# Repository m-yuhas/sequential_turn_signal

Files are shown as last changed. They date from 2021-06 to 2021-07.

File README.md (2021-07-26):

# Sequential Turn Signal
[中文指南](https://github.com/m-yuhas/sequential_turn_signal/blob/master/doc/读我档案.md)

[Documentación en español](https://github.com/m-yuhas/sequential_turn_signal/blob/master/doc/LÉAME.md)

[Documentation en français](https://github.com/m-yuhas/sequential_turn_signal/blob/master/doc/LISEZ-MOI.md)

## Introduction
On modern vehicles sequential turn signals are rapidly increasing in popularity.
A sequential turn signal is a turn signal which is divided into multiple
segments that illuminate in some dynamic pattern when the signal is activated.
While this functionality comes built in to many modern vehicles, this project
seeks to provide a simple method to introduce this functionality to classic cars
without having to replace the existing turn signal lights.  The software and
hardware are configured by default for a vehicle with three independent rear
turn signal lamps on each side of the vehicle, but can be adapted for other
configurations if needed.

If you plan to install this system on your vehicle, please read this entire
guide and understand what tools and skills you will need to complete this
project before beginning.  A high level of automotive and electronics experience
is recommended as this system has not yet been tested in an operating
environment.  Furthermore, it was designed for a specific vehicle and
modifications may be required to use it in another.

Please check the local regulations regarding modifications to vehicles before
starting.  This system will also introduce sequential behavior when the break
lights first illuminate, which may or may not be legal in your jurisdiction.
Additionally please understand the risks to yourself, your vehicle, and those
with whom you share the road.  These include, but are not limited to
electrocution, fire, messing up your vehicle's wiring harness, and ending up
with a vehicle with no working turn signals or break lights.  Proceed at your
own risk.

## Building the System
This system is composed of three components: a PCB with the microcontroller and
electronics; firmware, which runs on the microcontroller; and an enclosure to
offer some protection for the functional components of the system.  Each of the
sections below contains more details about each component, how to build it, and
some possible modifications.

### PCB
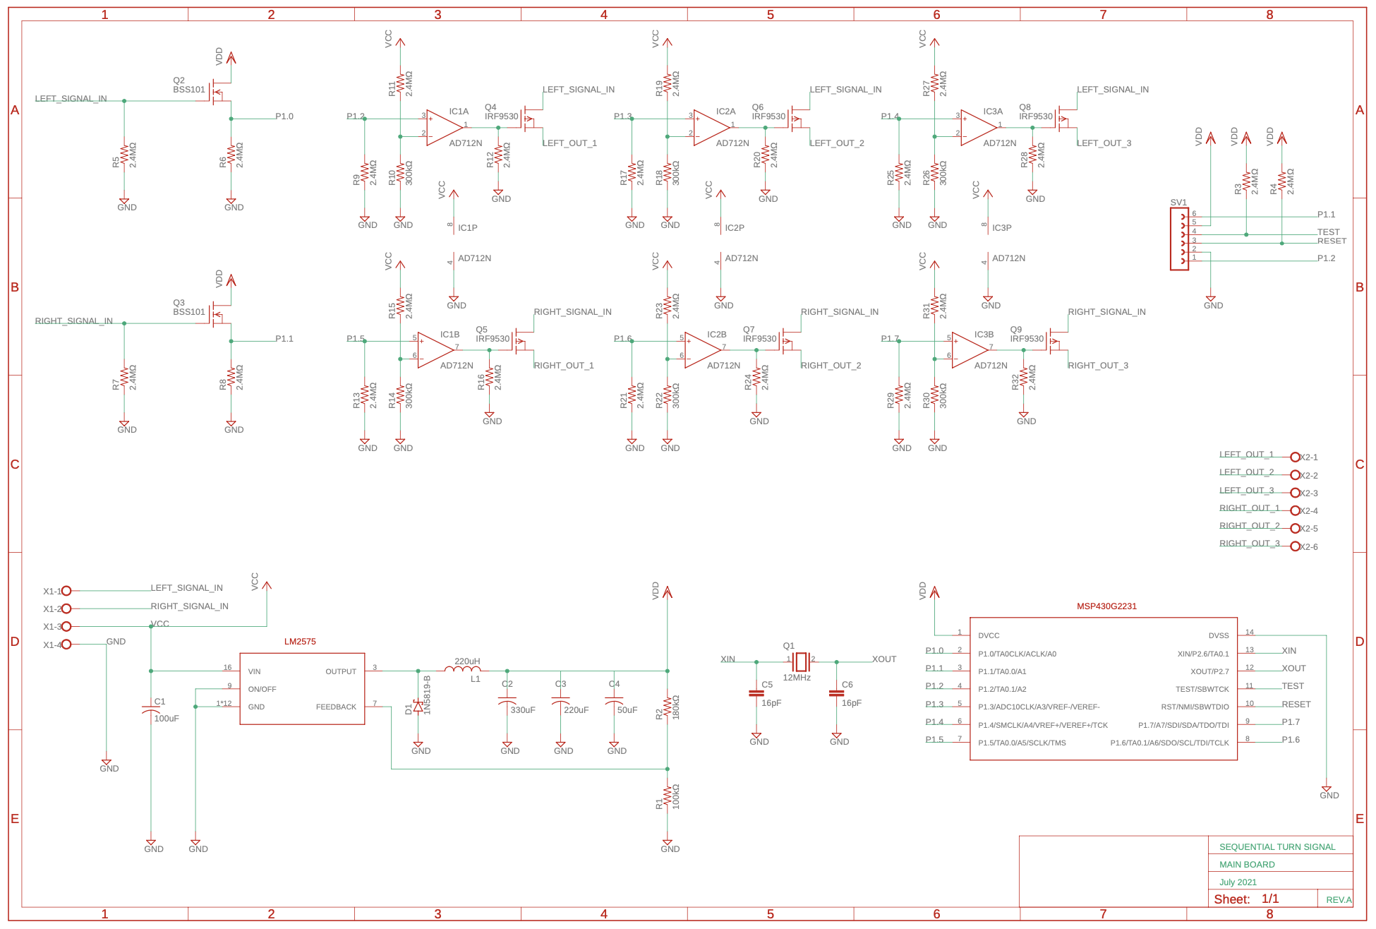
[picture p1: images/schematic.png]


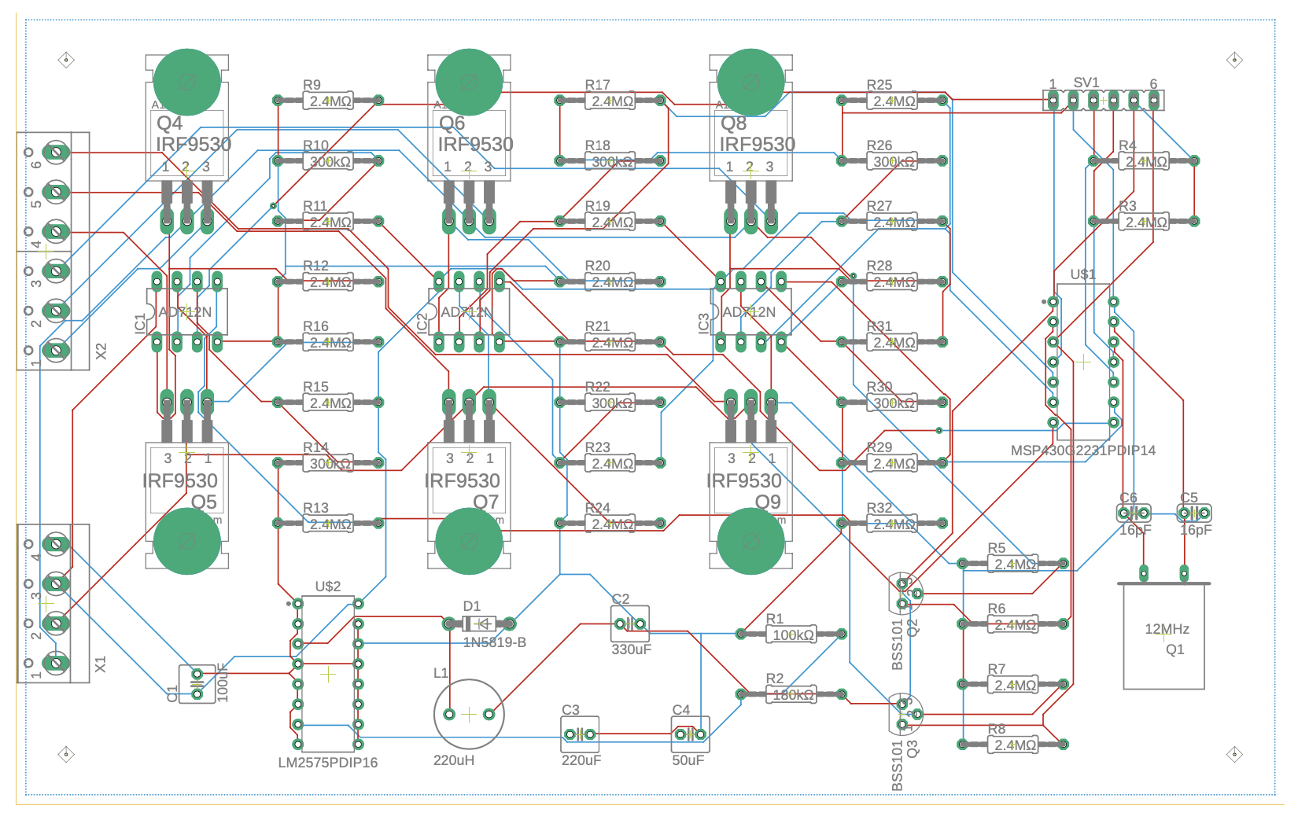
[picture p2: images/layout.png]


The schematic and PCB were created with
[EAGLE](https://www.autodesk.com/products/eagle/overview?term=1-YEAR). The
project can be loaded from the files in this repository's pcb folder.  Here are
the steps to build:
1. Use EAGLE to export Gerber files from the main.brd file.  You can follow
  [these instructions](https://www.autodesk.com/products/eagle/blog/gerber-nc-drill-pcb-manufacturing-basics-1/) from Autodesk.
2. Find a PCB manufacturer and send the Gerber files and Excellon drill files
  for manufacture.
3. You should receive a blank PCB from the manufacturer.  All the components
  were selected as through-hole to make home assembly easier.  You will need to
  purchase all the parts by model number as shown on the schematic.
4. Solder the components to the PCB.

Some things to consider:
1. This PCB intercepts the right and left turn signal lines and splits each into
  three signals lines for each individual lamp.  Assuming 30 Watt brake lamps,
  some of these traces will be passing up to 2.5 Amps, so if possible it is
  recommended to widen some of these traces to reduce resistance and mitigate
  the risk of thermal failure of the PCB.
2. The connectors for power, ground, input, and output are not automotive grade.
  They were selected as screw-in connectors to make debugging easier.  These
  should be replaced with proper connectors if possible.
3. The PCB layout contains sufficient space for a toroidal inductor for the
  switched mode power supply.  If you plan on making your own inductor, you can
  calculate the number of turns required using [this guide](http://www.nessengr.com/technical-data/toroid-inductor-formulas-and-calculator/).
  Remember to choose a wire thick enough to support up to 1 Amp.

### Software
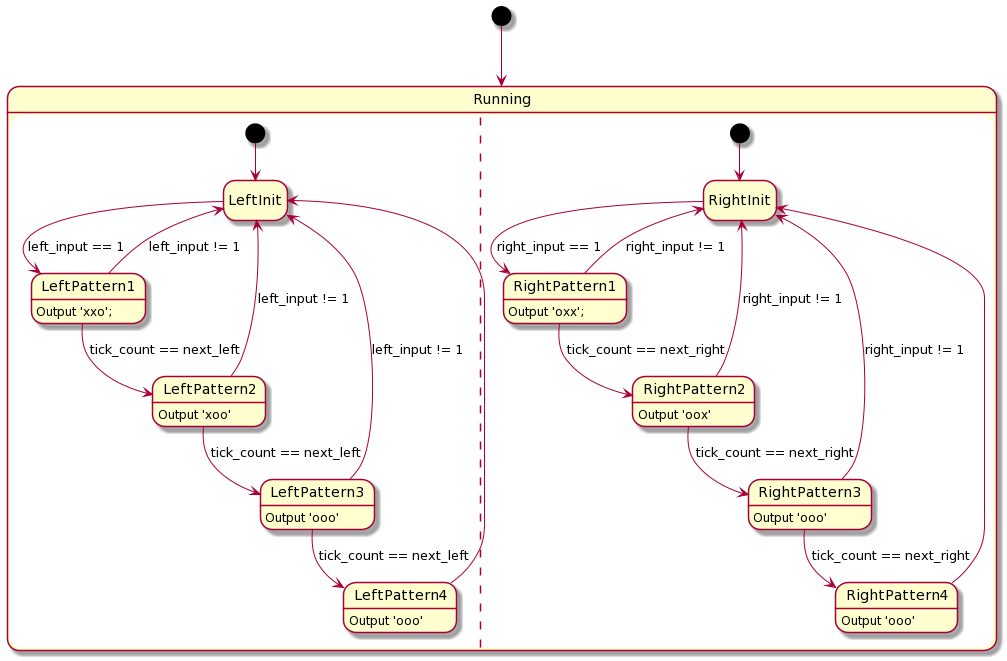
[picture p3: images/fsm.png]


The software component is composed of two finite state machines running on an
MSP430 microcontroller.  There is one FSM for each turn signal: when the input
signal line goes high, the FSM begins traversing through the output pattern
vectors with transitions based on times.  Once the input signal line goes low,
the FSM is reset.

The software was created with TI's [Code Composer Studio](https://www.ti.com/tool/CCSTUDIO).
You can load the project with the files in this repository's firmware folder.
Here are the steps to compile the firmware and load it on the PCB:
1. Buy an [MSP430 programmer](https://www.ti.com/tool/MSP-FET).
2. Open the Code Composer Studio project in this repository's firmware folder.
3. Connect the programmer to the debug header on the PCB.  The PCB's debug
  header is designed to communicate with the programmer using SBW and UART.
4. Follow the instructions in the [Code Composer Studio manual](https://www.ti.com/lit/ug/spru509h/spru509h.pdf)
  to flash the device.
5. When power is introduced on the PCB's 12 V power supply input, the MSP430
  should boot.  You can verify functionality by supplying 12 V to either left or
  right signal inputs and monitoring the voltages on the output pins.

Some things to consider:
1. You can define custom patterns using the macros at the top of the main.c file
2. You can speed up or slow down the sequential pattern by changing the
  definition of TIMER_RESOLUTION_TICKS in main.c
3. The version of the MSP430 used in this project only has one 8-bit port.  If
  your vehicle has more than six individual lamps (3 per side) that need to be
  controlled, you will need to select a different microcontroller and redesign
  the PCB.

### Enclosure
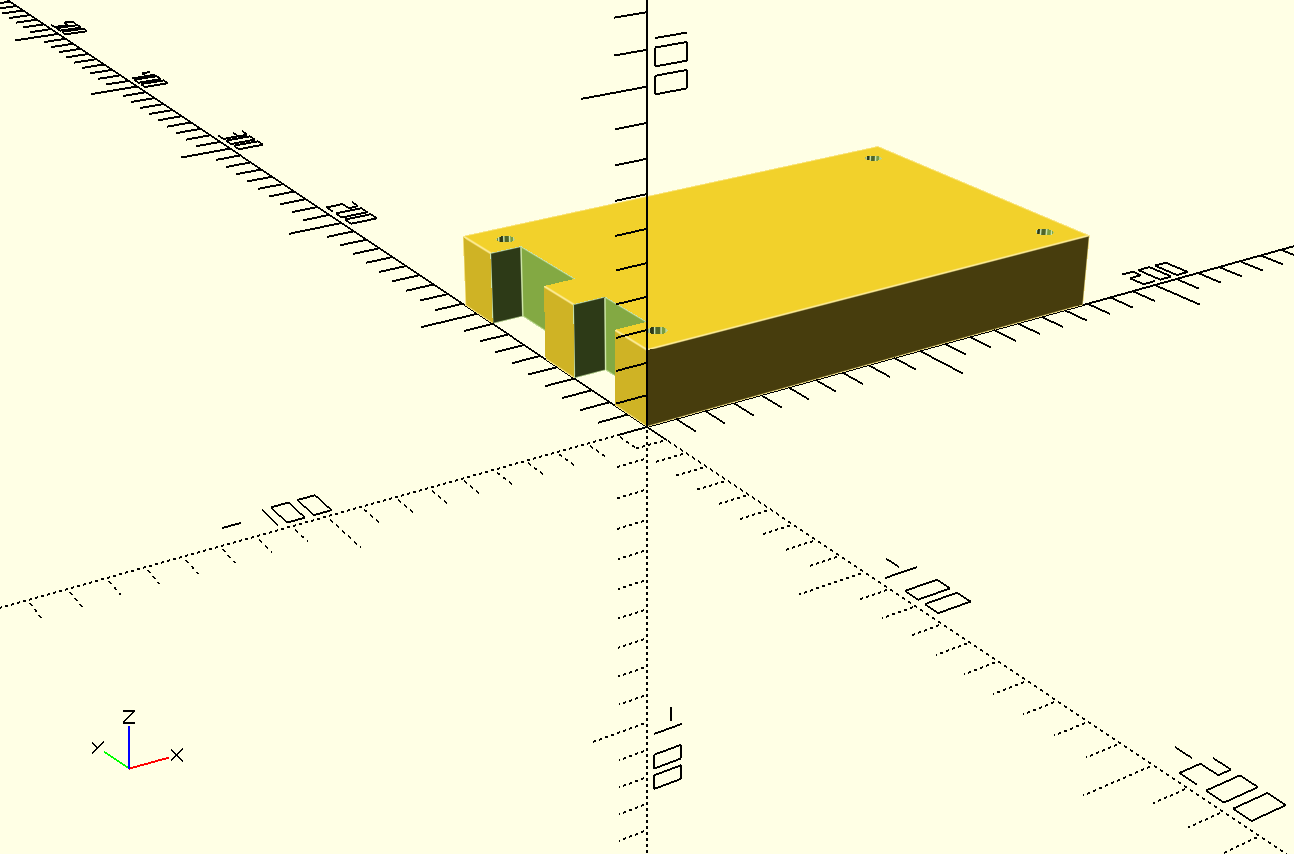
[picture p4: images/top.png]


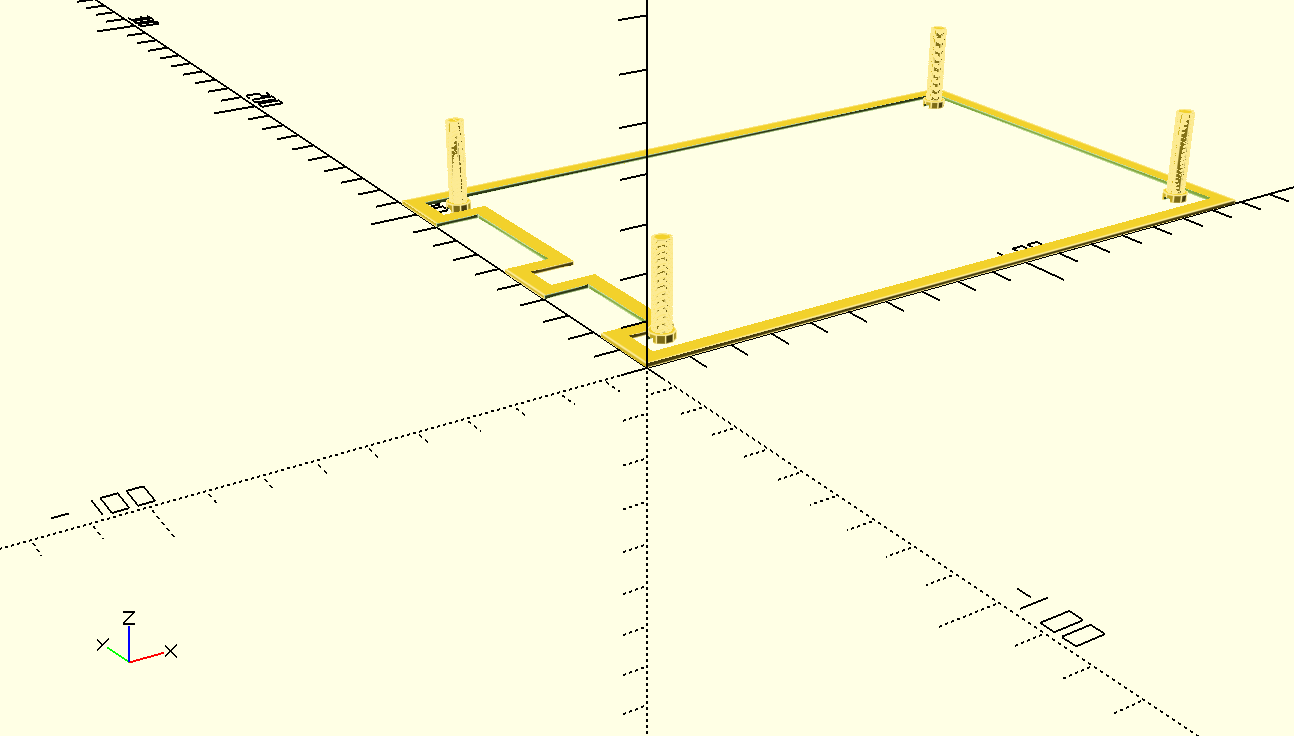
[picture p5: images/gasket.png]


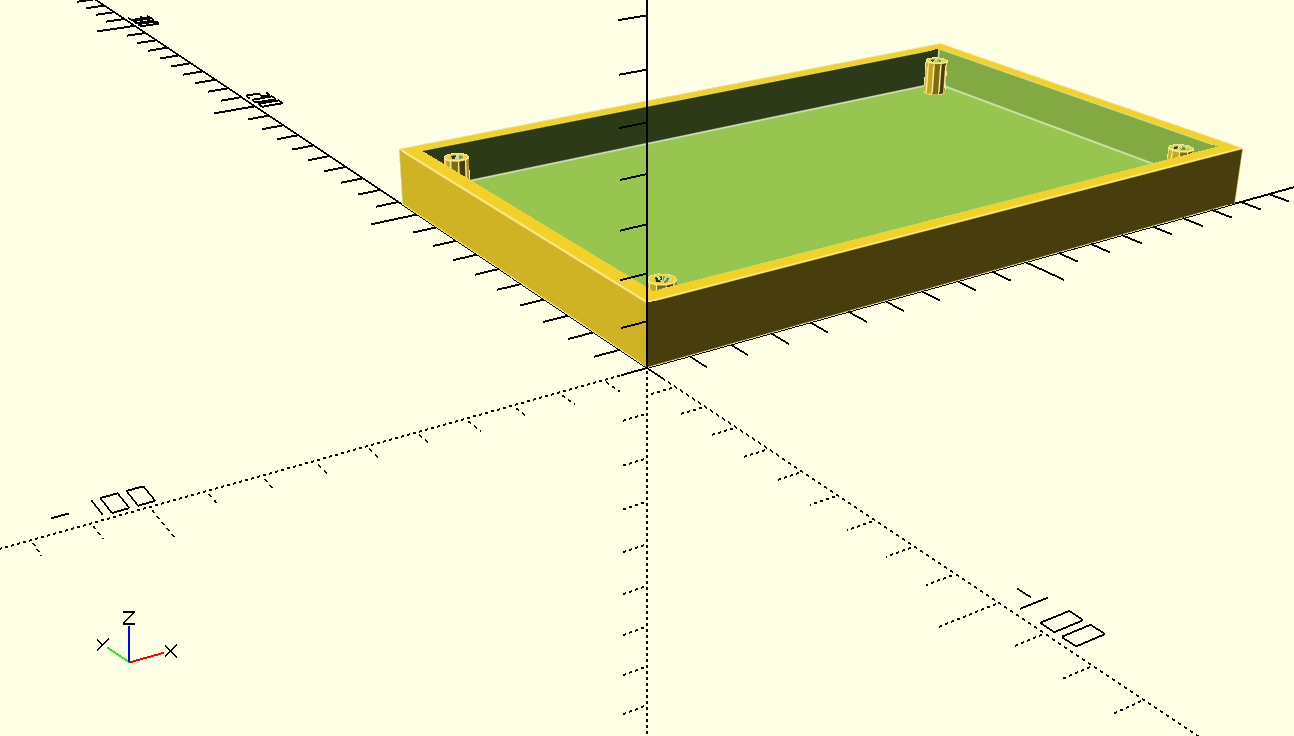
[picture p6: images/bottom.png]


The enclosure was designed using [OpenSCAD](https://openscad.org/).  This is not
a weatherproof design and the goal is to provide a minimum level of protection
for the PCB.  As such, it is recommended to install the enclosure in the
interior of the vehicle.

The enclosure CAD drawings are meant as a rough guide.  You can machine your own
metal enclosure based on the the drawings or convert them to STL files and 3D
print the pieces.  If the enclosure is 3D printed, please ensure that a plastic
is used which can handle the thermal extremes that can be found inside a
vehicle.

## Installing the System
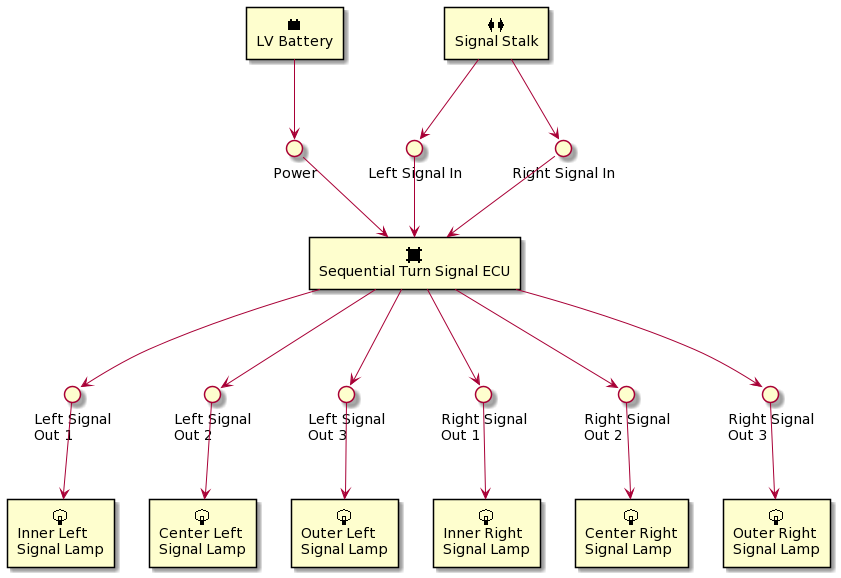
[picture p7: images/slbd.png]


The system has the following connections with the vehicle's wiring:
* **Power** - 12 V from the vehicle's low voltage battery.  Ideally this should
  come from a line that is high when the system is needed and low when the
  vehicle is parked for long durations.  This is because the microcontroller
  will be running anytime voltage is supplied on this input and could drain the
  battery if the vehicle is parked for a long time.  
* **Ground** - Vehicle ground; this can be connected to the vehicle chassis.
* **Right signal in** - Vehicle's original 12 V line to the right turn signal.
* **Left signal in** - Vehicle's original 12V line to the left turn signal.
* **Right signal out 1** - Connection between the system and the rear inner
  right turn signal lamp.
* **Right signal out 2** - Connection between the system and the rear center
  right turn signal lamp.
* **Right signal out 3** - Connection between the system and the rear outer
  right turn signal lamp.
* **Left signal out 1** - Connection between the system and the rear inner left
  turn signal lamp.
* **Left signal out 2** - Connection between the system and the rear center left
  turn signal lamp.
* **Left signal out 3** - Connection between the system and the rear outer left
  turn signal lamp.

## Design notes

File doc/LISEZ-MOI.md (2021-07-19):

# Clignotant Séquentiel

## Introduction
Dans les véhicules modernes les clignotants séquentiels s'accroissent rapidement
leur popularité.  Un clignotant séquentiel est un clignotant lequel est divisé
en segments plusiers que s'éclairent en motif dynamique quand le clignotant est
activé.  Tandis que cette fonctionnalité est déjà inclus en beaucoup des
véhicules modernes, ce project cherche à fournir une méthode simple pour
introduire cette fonctionnalité en voitures classiques sans la besoin de
remplacer tous les feux clignotants originals.  Le logiciel et le matériel sont
configurés par défaut pour un véhicule avec trois feux clignotants arrières
indépendants de chaque côté du véhicule, mais il peut être adapté pour autres
configurations s'il est nécessaire.

Si vous planifiez installer ce système dans votre véhicule, s'il vous plaît
lisez ce guide entièrement et comprenez vous aurez besoin de quels outils et
compétences avant de commencer.  Un niveau élevé d'expérience automobile et
électronique est recommandé comme ce système n'a pas été testé dans un
environnement opérationnel.  En outre, il est conçu pour un véhicule spécifique
et peut-être modifications seront requis si vous voudriez l'utiliser dans un
autre.

S'il vous plaît vérifiez les réglementations locales concernant modifications
aux véhicules avant de commencer.  Ce système aussi introduira le comportement
séquentiel au début de l'éclairage des feux stop, lequel est peut-être ou
pas peut-être légal dans votre jurisdiction.  Aditionellement s'il vous plaît
comprenez les risques à vous-même, à votre véhicule, et aux autres gens avec qui
vous partagez la route.  Ces incluent, mais ne sont pas limités à la
électrocution, au feu, à ruinant le faisceau de câblage de votre véhicule, et
à finissant avec un véhicule que n'a pas des feux clignotants ou des feux stop
fonctionnels.  Procédez à votre risque.

## Construire le Système
Ce système est composé de trois composants: un circuit imprimé avec le
microcontrôleur et l'électronique; le micrologiciel, lequel exécute dans le
microcontrôleur; et un boîtier pour offrir de protection à les composants
fonctionnels du système.  Chacun des sections suivantes contient plus de détails
sur chaque composant, comment le construire, et des modifications possibles.

### Circuit Imprimé
Téléchargement en cours...

Téléchargement en cours...

Le diagramme schématique et le circuit imprimé ont été créés avec
[EAGLE](https://www.autodesk.com/products/eagle/overview?term=1-YEAR).  Le
projet peut être chargé des fichiers dans le répertoire 'pcb' de ce dépôt.
Voici les étapes pour le construire:
1. Utilisez EAGLE à exporter les fichiers Gerber du fichier main.brd.  Vous
  pouvez suivre [ces instructions](https://www.autodesk.com/products/eagle/blog/gerber-nc-drill-pcb-manufacturing-basics-1/)
  d'Autodesk.
2. Trouvez un fabricant des circuits imprimés et les envoyez les fichiers Gerber
  et les fichiers Excellon pour fabrication.
3. Vous devez recevoir un circuit imprimé vide du fabricant.  Tous les
  composants ont été sélectionnés comme les composants de trou traversant pour
  faire l'assemblage chez vous plus facile.  Vous aurez besoin d'acheter tous
  les composants par numéro de modèle comme il est montré dans le diagramme
  schématique.
4. Soudez les composants au circuit imprimé.

Des choses à considérer:
1. Ce circuit imprimé intercepte les lignes clignotants droit et gauche et les
  divise en trois lignes de signal pour chaque lampe individuelle.  Supposant
  lampes de stop de 30 watts, quelques traces porteront jusqu'à 2.5 ampères,
  alors s'il est possible il est recommandé à élargir ces traces pour réduire
  leurs résistances et atténuer le risque d'échec thermique du circuit imprimé.
2. Les connecteur pour l'alimentation, la terre, l'entrée, et la sortie ne sont
  pas de qualité automobile.  Ils ont été sélectionnés comme connecteurs de vis
  pour faire la débogage plus facile.  Ces doivent être remplacés avec des
  connecteurs appropriés s'il est possible.
3. Le circuit imprimé contient l'espace suffisant pour un inducteur toroïdal
  pour l'alimentation à découpage.  Si vous planifiez en faisant votre propre
  inducteur, vous pouvez calculer le numéro de tours requis en utilisant
  [ce guide](http://www.nessengr.com/technical-data/toroid-inductor-formulas-and-calculator/).
  Rappelez-vous choisir un fil suffisamment large pour soutenir jusqu'à 1
  ampère.

### Logiciel
Téléchargement en cours...

Le composant logiciel est composé de deux automates fini lesquels exécutent sur
un microcontrôleur MSP430.  Il y a un automate fini pour chaque clignotant:
lorsque la ligne du signal de l'entrée va à l'haute, l'automate fini commence à
traverser les vecteurs du motif de la sortie avec transitions basé sur temps.
Une fois que la ligne du signal de l'entrée va à la basse, l'automate fini se
réinitialise.

Le logiciel a été créé avec le [Code Composer Studio](https://www.ti.com/tool/CCSTUDIO)
de TI. Vous pouvez charger le projet avec les fichiers dans le répertoire
'firmware' de ce dépôt.  Voici les étapes pour compiler le micrologiciel et le
charger sur le circuit imprimé:
1. Achetez un [programmeur MSP430](https://www.ti.com/tool/MSP-FET).
2. Ouvrez le project de Code Composer Studio dans le répertoire 'firmware' de ce
  dépôt.
3. Connectez le programmeur au connecteur de débogage du circuit imprimé.  Le
  connecteur de débogage du circuit imprimé est conçu pour communiquer avec le
  programmeur en utilisant SBW et UART.
4. Suivez les instructions dans le [manuel de Code Composer Studio](https://www.ti.com/lit/ug/spru509h/spru509h.pdf)
  pour charger le micrologiciel au appareil.
5. Quand le pouvoir est introduit dans l'entrée de l'alimentation 12 V du
  circuit imprimé, le MSP430 devrait se démarrer.  Vous pouvez vérifier le
  fonctionnalité en fournissant 12 V à chacun des entrées des clignotants gauche
  ou droit et en surveillant les tensions sur les goujons de sortie.

Des choses à considérer:
1. Vous pouvez définir motifs à la mode en utilisant les macros à la tête du
  fichier main.c.
2. Vous pouvez accélérer ou ralentir le motif séquentiel en changeant la
  définition de TIMER_RESOLUTION_TICKS dans main.c.
3. La version du MSP430 laquelle est utilisée en ce projet seulement a un port
  8-bit.  Si votre véhicule a plus que six lampes individuelles (3 par côté)
  qu'ont besoin d'être contrôlées, vous aurez besoin de sélectionner un
  microcontrôleur différent et repenser le circuit imprimé.

### Boîtier
Téléchargement en cours...

Téléchargement en cours...

Téléchargement en cours...

Le boîtier a été conçu avec [OpenSCAD](https://openscad.org/).  Ceci n'est pas
une conception imperméable et le but est apporter un niveau minimum de
protection pour le circuit imprimé.  Comme tel, il est recommandé à installer le
boîtier dans l'intérieur du véhicule.

Les dessins de CAO du boîtier sont proposés comme un guide approximatif.  Vous
pouvez usiner votre propre boîtier de métal basé sur les dessins ou les
convertir en fichiers de STL et imprimer en 3D les pièces.  Si le boîtier est
imprimé en 3D, s'il vous plaît vous assurez que vous utilisiez un plastique que
puisse résister les extrêmes thermiques qu'on peut trouver dans un véhicule.

## Installation du Système
Téléchargement en cours...

Le système a les connexions suivantes avec le câblage du véhicule:
* **Pouvoir** - 12 V de la pile de basse tension du véhicule.  Idéalement ce
  devrait venir d'une ligne laquelle est haute lorsque le véhicule a besoin du
  système et basse lorsque le véhicule est stationné pour longtemps.  C'est
  parce que le microcontrôleur fonctionnera quand la tension est fournie à cette
  entrée et pourrait drainer la pile si le véhicule reste stationné pour
  longtemps.
* **Terre** - La terre du véhicule; ceci peut être rattachée au châssis du
  véhicule.
* **Entrée de clignotant droit** - La ligne 12 V originalement au clignotant
  droit du véhicule.
* **Entrée de clignotant gauche** - La ligne 12 V originalement au clignotant
  gauche du véhicule.
* **Sortie de clignotant droit 1** - Le lien entre le système et la lampe de
  clignotant droit arrière de dedans.
* **Sortie de clignotant droit 2** - Le lien entre le système et la lampe de
  clignotant droit arrière du milieu.
* **Sortie de clignotant droit 3** - Le lien entre le système et la lampe de
  clignotant droit arrière d'extérieur.
* **Sortie de clignotant gauche 1** - Le lien entre le système et la lampe de
  clignotant gauche arrière de dedans.
* **Sortie de clignotant gauche 2** - Le lien entre le système et la lampe de
  clignotant gauche arrière du milieu.
* **Sortie de clignotant gauche 3** - Le lien entre le système et la lampe de
  clignotant gauche arrière d'extérieur.

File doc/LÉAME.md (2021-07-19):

# Intermitente Secuencial

## Introducción
En vehículos modernos intermitentes secuenciales se están creciendo rápidamente
su popularidad. Un intermitente secuencial es un intermitente cual es dividido
en segmentos múltiples que se iluminan en un patrón dinámico cuando la señal
está activada.  Mientras esta funcionalidad ya es incorporada en muchos
vehículos modernos, este proyecto busca proprocionar un método sencillo para
introducir esta funcionalidad en coches clásicos sin necesitando la remoción de
los intermitentes originales.  El software y el hardware son configurados por
defecto para un vehículo con tres lámparas de intermitente trasero
independientes en cada lado del vehículo, pero pueden estar adaptados para
configuraciones otras si es necesario.

Si planifica usted instalar este sistema en su vehículo, por favor lea esta guía
enteramente y comprenda que son las herramientas y las habilidades requeridas
para completar este proyecto antes de empezar.  Un nivel altíssimo de
experiencia automotriz y electrónica es recomendado como este sistema ya no ha
probado en un medio ambiente operacional.  Además, no estaba diseñado para un
vehículo específico y tal vez modificaciones son necesarios para usarlo en otro
vehículo.

Por favor verifique las regulaciones locales con respecto a modificaciones de
vehículos antes de empezar.  Este sistema también introducirá el funcionamiento
secuencial cuando las luces de freno iluminar al principio, cual podría o no
podría ser legal en su jurisdicción.  Adicionalmente por favor comprenda los
riesgos a su mismo, su coche, y la gente con quién comparte el camino.  Estos
riesgos incluyen, pero no se limitan a electrocución, fuego, estropeando el
arnés de cableado de su vehículo, y acabando con un vehículo con intermitentes o
luces de freno que no funcionan.  Proceda a su mismo riesgo.

## Construir el Sistema
Este sistema consiste de tres componentes: una placa de circuito impreso con
un microcontrolador y la electrónica; firmware, cual ejecuta en el
microcontrolador; y una caja para ofrecer alguna protección para los componentes
funcionales del sistema.  Cada de las secciones siguientes contiene más detalles
sobre cada componente, cómo construirlo, y unas modificaciones posibles.

### Placa de Circuito Impreso
Cargando...

Cargando...

El esquematismo y la placa de circuito impreso estaban creados con
[EAGLE](https://www.autodesk.com/products/eagle/overview?term=1-YEAR). El
proyecto puede estar cargado de los archivos en la carpeta de 'pcb' en este
repositorio.  Aquí son los pasos para construirlo:
1. Use EAGLE para exportar los archivos Gerber del archivo main.brd.  Usted
  puede seguir [estas instrucciones](https://www.autodesk.com/products/eagle/blog/gerber-nc-drill-pcb-manufacturing-basics-1/) de Autodesk.
2. Encuentre un fabricante de placas de circuito impreso y le envíe al
  fabricante los archivos Gerber y los archivos Excellon para fabricarlos.
3. Debe recibir una placa de circuito impreso blanco del fabricante.  Todos los
  componentes estaban seleccionados como tecnología de agujeros pasantes para
  hacer el montaje en casa más fácil.  Necesitará comprar todas las partes por
  el número de modelo como se muestra el esquematismo.
4. Suelde los componentes en la placa de circuito impreso.

Algunas cosas para considerar:
1. Esta placa de ciruito impreso intercepta las líneas de los intermitentes
  derechos e izquierdos y separa cada en tres señales, una para cada lámpara
  individual.  Si asumimos una lámpara de freno consume 30 vatios, unos de estos
  rastros pasarán hasta 2.5 amperios. Así si es posible es recomendado ensanchar
  unos de estos rastros para reducir la resistencia y mitigar el riesgo del
  fracaso térmico de la placa de circuito impreso.
2. Los conectores para el poder, la tierra, la entrada, y la salida no son de la
  calidad automatriz.  Estaban seleccionados como conectores de tornillo para
  hacer más fácil la depuración.  Deben estar reemplazados con conectores
  adecuados si es posible.
3. El arreglo de la placa de circuito impreso contiene espacio suficiente para
  un inductor toroidal para el fuente conmutada.  Si planifica hacerse su propio
  inductor, puede calcular el número de veultas requeridas usando [esta guía](http://www.nessengr.com/technical-data/toroid-inductor-formulas-and-calculator/).
  Recuerda escoger un alambre lo suficiente ancho para llevar hasta 1 amperio.

### Software
Cargando...

El componente software se compone de dos autómatas finitos que ejecutan en un
microcontrolador MSP430.  Hay un autómata finito para cada intermitente: cuando
la línea de señal entrada va arriba, el autómata finito empieza atravesar los
vectores de patrones salidos con transiciones basadas en tiempos.  Una vez la
línea de señal entrada va abajo, el autómata finito se reinicia.

El software estaba creado usando el [Code Composer Studio](https://www.ti.com/tool/CCSTUDIO)
de TI.  Usted puede cargar el proyecto con los archivos en la carpeta de
'firmware' de este repositorio.  Aquí están los pasos para compilar el firmware
y cargarlo en la placa de circuito impreso:
1. Compre un programador [programador MSP430](https://www.ti.com/tool/MSP-FET).
2. Abra el proyecto de Code Composer Studio en la carpeta de 'firmware' de este
  repositorio.
3. Conecte el programdor al conector de depuración en la placa de circuito
  impreso.  El conector de depuración en la placa de circuito impreso estaba
  diseñado para comunicar al programador usando SBW y UART.
4. Siga las instrucciones en el [manual del Code Composer Studio](https://www.ti.com/lit/ug/spru509h/spru509h.pdf)
  para cargar el firmware en el dispositivo.
5. Cuando introduzca el poder a la entrada del fuente de poder de 12 V de la
  placa de circuito impreso, el MSP430 debe iniciar.  Puede verificar la
  funcionalidad en proveyendo 12 V a la entrada de señal izquierda o la entrada
  de señal derecha y observando los voltajes en las clavijas salidas.

Unas cosas para considerar:
1. Puede definir los patrones a medida usando las macros en el principio del
  archivo main.c
2. Puede acelerar o desacelerar los patrones secuenciales en cambiando la
  definición de TIMER_RESOLUTION_TICKS en main.c
3. La versión del MSP430 cual estaba usada en este proyecto solo tiene uno
  puerto 8-bit.  Si su vehículo tiene más que seis lámparas individuales (tres
  por lado) que necesitan ser controladas, necesite seleccionar un
  microcontrolador diferente y rediseñar la placa de circuito impreso.

### Caja
Cargando...

Cargando...

Cargando...

La caja estaba diseñada usando [OpenSCAD](https://openscad.org/).  No es un
diseño impermeabilizado y la meta es provee un nivel de protección mínimo para
la placa de circuito impreso.  Por ello, es recomendado instalar la caja el el
interior del vehículo.

Los dibujos CAD de la caja sirven de una guía aproximada.  Puede fabricar a
máquina su propio caja metal basado en los dibujos o convertirlos en archivos
de STL e imprimirlos en 3D.  Si imprime en 3D la caja, por favor se asegure que
use un plástico que puede manejar los extremos térmicos que puede encontrar en
un vehículo.

## Instalar el Sistema
Cargando...

El sistema tiene las conexiones siguientes con el cableado del vehículo:
* **Poder** - 12 V de la pila de baja tensión del vehículo.  Idealmente debe
  venir de una línea que es alta cuando el sistema esté necesitado y bajo cuando
  el vehículo esté estacionado por duraciones largas.  Este es porque el
  microcontrolador funcionará en cualquier momento que hay un voltaje en esta
  entrada y podría vaciar la pila si el vehículo quede estacionado por mucho
  tiempo.
* **Tierra** - la tierra del vehículo; esta puede ser conectada al chasis del
  vehículo.
* **Entrada del intermitente derecho** - La línea de 12 V originalmente al
  intermitente derecho del vehículo.
* **Entrada del intermitente izquierdo** - La línea de 12 V originalmente al
  intermitente izquierdo del vehículo.
* **Salida del intermitente derecho 1** - La conexión entre el sistema y la
  lámpara del intermitente derecho trasero más interno.
* **Salida del intermitente derecho 2** - La conexión entre el sistema y la
  lámpara del intermitente derecho trasero medio.
* **Salido del intermitente derecho 3** - La conexión entre el sistema y la
  lámpara del intermitente derecho trasero periférico.
* **Salida del intermitente izquierdo 1** - La conexión entre el sistema y la
  lámpara del intermitente izquierdo trasero más interno.
* **Salida del intermitente izquierdo 2** - La conexión entre el sistema y la
  lámpara del intermitente izquierdo trasero medio.
* **Salido del intermitente izquierdo 3** - La conexión entre el sistema y la
  lámpara del intermitente izquierdo trasero periférico.

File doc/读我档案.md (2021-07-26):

# 序列性转向灯

## 介绍
在现代的车辆序列性转向灯越来越热门。序列转向灯是一盏段节的转向灯、转向灯激活的时候段节照明根据动
态格局。鉴于这个功能已经内置很多现代车辆，这个项目谋求提供一个简单办法导入这个功能在老爷车、尤其
没有更换现有的转向灯的要求。这个项目的软件与硬件预设为一辆有三盏转向灯在车辆左边和右边的车，但是
如果需要就它们会被适应配合其他位形。

如果您安排安装这个系统在您的车辆里面，请仔细阅读整个指南开始以前还要明白您需要什么工具与技能为完
成这个项目。因为这个系统还没被测试在操作环境中所以它需要高级车辆与电器经验。而且它被设计为一辆特
定车辆、如果您想用它在其他车辆里就需要修改设计。

请参考本地法律对于变更私人车辆开始以前。这个系统也导入序列性性质当刹车灯起初照明，这个功能可否合
法在您本地司法权下。另外请完全明白所有风险：对于自己、对于您的车辆、并且对于那些跟您分享马路的人
。这些风险包括（但是不限于）：电死、火灾、搞砸车辆的布线、并且完成后没有一辆有可用的转向灯和刹车
灯的车辆。请记得套期保值。

## 建立系统
这个系统有三个零件：一块印刷电路板（包含单片机和电子机器）、一个韧体（在单片机执行的）、一个机箱
（为保护系统的功能零件）。每个随着的阶段包括更多详细关于系统的每个零件、怎么建立、还有一些可能变
更。

### 印刷电路板
下载中。。。

下载中。。。

示意图被绘图使用
[EAGLE](https://www.autodesk.com/products/eagle/overview?term=1-YEAR)。示意图会被
调入用这个仓库的pcb目录的档案。这里有建立的步骤：
1. 使用EAGLE为汇出Gerber档案从项目main.brd档案。您会跟随
  [这些从Autodesk的指示](https://www.autodesk.com/products/eagle/blog/gerber-nc-drill-pcb-manufacturing-basics-1/)。
2. 找一个印刷电路板的厂商就把Gerber和Excellon档案发送它为制作。
3. 您应该从厂商获得一块空的印刷电路板。所有的零件被选择为通孔插装技术零件为使生产在家里更容易。
  您需要买所有的零件用在示意图上的型号。
4. 烙铁所有的零件对印刷电路板。

一些要考虑的事项：
1. 这个印刷电路板把右边和左边转向灯信号拦截和分每一个成为三个线、一线一灯。假设三十瓦特刹车灯泡
  就有一些线需要扶持直到2.5安培，因此加宽印刷电路板的线为减少电阻和疏解热性故障风险是推荐的。
2. 电源、接地、输入、输出的连接器都不算车辆等级品。它们被选择作为螺丝连接器为使调试更容易。如果
  可以就使用合适的连接器代替预设连接器。
3. 印刷电路板的布局包含足够空间使用一台环状感应器在开关模式电源里。如果您安排绕自己的感应器就可
  以使用[这个指南](http://www.nessengr.com/technical-data/toroid-inductor-formulas-and-calculator/)
  为算需要多少转。记得选择一条够宽的线位支持至少1安培。

### 软件
下载中。。。

两个有限状态机执行在一个MSP430单片机上构成系统的软件零件。每个转向灯有一个有限状态机：当输入信
号线往上时，状态机就开始遍历输出格局向量根据定时器中断。当输入信号线往下时，有限状态机就重启自
己。

这个软件被开发使用德州仪器的[Code Composer Studio](https://www.ti.com/tool/CCSTUDIO)。
您可以载入这个项目用这个仓库的firmware目录的档案。这里有步骤为编译韧体就把二进制文件刷在印刷电
路板上：
1. 买一个[MSP430编程机器](https://www.ti.com/tool/MSP-FET)。
2. 打开这个仓库的firmware目录的Code Composer Studio项目。
3. 连线编程机器对印刷电路板的调试接口。印刷电路板的调试接口使用SBW和UART沟通编程机器。
4. 跟随[Code Composer Studio的说明书](https://www.ti.com/lit/ug/spru509h/spru509h.pdf)
  的详细为刷单片机。
5. 当您提供十二伏特在印刷电路板的电源输入时，MSP430就应该启动。您可以提供十二伏特在左边或者右
  边转向灯信号输入和监控输出的电压为确认它的功能。

一些要考虑的事项：
1. 您可以使用在main.c档案的巨集为定义专门输出格局。
2. 您可以改变main.c档案的TIMER_RESOLUTION_TICKS变量为加速或者减速序列性的格局。
3. 这个项目的MSP430版本只有一个八位元的接口。如果您的车辆有更多转向灯泡比六个（三泡一边），就
  需要选择新的单片机和再设计印刷电路板。

### 机箱
下载中。。。

下载中。。。

下载中。。。

这个机箱被设计用[OpenSCAD](https://openscad.org/)。这个机箱不防天气、目标仅是提供最少的保
护水平为印刷电路板。因此推荐安装机箱在车辆内部里面。

机箱的计算机辅助设计图纸作为大概攻略。您可以铣自己的金属机箱跟随图纸或者转换图纸为STL档案就3D
打印块们。如果机箱被3D打印的，请确定使用一个可以弄车辆里面热性极限的塑料。

## 安装系统
下载中。。。

这个系统有以下的链接跟车辆的布线：
* **电源：** 十二伏特从车辆低压电池。标称这个应该从一条高当系统需要运行时和低当停车长时间时的
  线。缘故是单片机有电源时它就运行、如果车辆停车长时间这个可能会浪费低压电池。
* **接地：** 车辆接地；推荐链接车架。
* **右边转向灯输入：** 车辆原来十二伏特线向右转向灯。
* **左边转向灯输入：** 车辆原来十二伏特线向左转向灯。
* **右边转向灯输出一：** 系统和后内右转向灯泡之间的链接。
* **右边转向灯输出二：** 系统和后中右转向灯泡之间的链接。
* **右边转向灯输出三：** 系统和后外右转向灯泡之间的链接。
* **左边转向灯输出一：** 系统和后内左转向灯泡之间的链接。
* **左边转向灯输出二：** 系统和后中左转向灯泡之间的链接。
* **左边转向灯输出三：** 系统和后外左转向灯泡之间的链接。

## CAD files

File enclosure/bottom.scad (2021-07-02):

/* Bottom portion of the enclosure for:
 * Sequential Turn Signal
 *
 * This part can be constructed out of metal, plastic, or wood,
 * but metal is recommended.  The enclosure should be mounted in
 * a dry, well-ventilated area as it will not prevent moisture
 * ingress or provide thermal insulation for the electronics.
 */

include <MCAD/screw.scad>

inner_x = 160;          // Interior dimension of enclosure in x direction.
inner_y = 100;          // Interior dimension of enclosure in y direction.
inner_z = 10;           // Interior dimension of enclosure in z direction.
wall_d = 4;             // Enclosure wall thickness.
mount_r = 3;            // Radius of PCB mounting posts.
pcb_z = 1;              // PCB thickness.
screw_inset = 6;        // Distance from closest edge of PCB to center of screw.
thread_pitch = 0.25;    // Mounting screw thread pitch.
thread_outer_r = 2.182; // Mounting screw outer radius.
thread_inner_r = 1.911; // Mounting screw inner radius.
eps = 0.001;            // Epsilon constant to ensure overlap for difference().

// The bottom portion of the enclosure.
module bottom()
{

  // Mounting stub to attach the PCB to the bottom of the enclosure.
  module mount()
  {
    difference()
    {
      cylinder(r=mount_r, h=inner_z - pcb_z);
      auger(pitch=thread_pitch,
            length=inner_z - pcb_z + eps,
            outside_radius=thread_outer_r,
            inner_radius=thread_inner_r);
    }
  }

  // Interior volume of the bottom of the enclosure.
  module interior()
  {
    difference()
    {
      cube([inner_x, inner_y, inner_z + eps]);
      translate([screw_inset, screw_inset, 0]) mount();
      translate([inner_x - screw_inset, screw_inset, 0]) mount();
      translate([screw_inset, inner_y - screw_inset, 0]) mount();
      translate([inner_x - screw_inset, inner_y - screw_inset, 0]) mount();
    }
  }

  /* Construct the bottom portion of the enclosure by removing the interior
   * volume from the volume bounded by the exterior.
   */
  difference()
  {
    cube([inner_x + 2 * wall_d, inner_y + 2 * wall_d, inner_z + wall_d]);
    translate([wall_d, wall_d, wall_d]) interior();
  }

}

bottom();

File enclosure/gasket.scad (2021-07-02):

/* Gasket and screws for the enclosure for:
 * Sequential Turn Signal
 *
 * Ideally the equivalent screws are purchased an not self-fabricated
 * (ANSI/ASME B1.13M-1995 M2.2 x 0.25).  Ideally a silicon gasket will be used.
 */

include <MCAD/screw.scad>

inner_x = 160;          // Interior dimension of enclosure in x direction.
inner_y = 100;          // Interior dimension of enclosure in y direction.
gasket_d = 4;           // Minimum gasket thickness along the the x/y plane.
gasket_z = 1;           // Gasket height in z direction.
mount_r = 3;            // Radius of PCB mounting posts.
screw_inset = 6;        // Distance from closest edge of PCB to center of screw.
screw_r = 3;            // Screw head radius.
screw_h = 2;            // Height of screw head.
thread_h = 20;          // Height of the screw shaft.
thread_pitch = 0.25;    // Mounting screw thread pitch.
thread_outer_r = 2.182; // Mounting screw outer radius.
thread_inner_r = 1.911; // Mounting screw inner radius.
pwr_inset_x = 11;       // Size of power connector in x direction.
pwr_inset_y = 23;       // Size of power connector in the y direction.
pwr_offset = 13;        // Offset from origin along y axis to power connector.
sig_inset_x = 11;       // Size of signal connector in x direction.
sig_inset_y = 33;       // Size of signal connector in y direction.
sig_offset = 53;        // Offset from origin along y axis to signal connector.
eps = 0.001;            // Epsilon constant to ensure overlap for difference().

// Gasket to provide a seal between the top and bottom of the enclosure.
module gasket()
{

  // Exterior shell of the gasket.
  module exterior()
  {
    difference()
    {
      cube([inner_x + 2 * gasket_d, inner_y + 2 * gasket_d, gasket_z]);
      translate([-eps, pwr_offset + gasket_d, -eps]) {
        cube([pwr_inset_x + eps, pwr_inset_y, gasket_z + 2 * eps]);
      }
      translate([-eps, sig_offset + gasket_d, -eps])
      {
        cube([sig_inset_x + eps, sig_inset_y, gasket_z + 2 * eps]);
      }
    }
  }

  // Interior shell of the gasket.
  module interior()
  {
    difference()
    {
      cube([inner_x, inner_y, gasket_z + 2 * eps]);
      translate([-eps, pwr_offset - gasket_d, -2 * eps])
      {
        cube([pwr_inset_x + eps, pwr_inset_y + 2 * gasket_d, gasket_z + 4 * eps]);
      }
      translate([-eps, sig_offset - gasket_d, -2 * eps]) {
        cube([sig_inset_x + eps, sig_inset_y + 2 * gasket_d, gasket_z + 4 * eps]);
      }
    }
  }

  // Construct gasket by removing the interior volume from the exterior volume.
  difference()
  {
    exterior();
    translate([gasket_d, gasket_d, -eps]) interior();
  }

}

// Example of a screw compatible with this enclosure.
module screw()
{

  // Screw head.
  module head()
  {
    difference()
    {
      cylinder(r=screw_r, h=screw_h);
      translate([-screw_r - eps, -screw_h / 2, -eps]) {
        cube([2 * screw_r + 2 * eps, screw_h, screw_h / 2 + eps]);
      }
    }
  }

  // Screw shaft.
  module shaft()
  {
    translate([0, 0, screw_h - eps]) {
      auger(pitch=thread_pitch,
            length=thread_h + eps,
            outside_radius=thread_outer_r,
            inner_radius=thread_inner_r);
    }
  }

  // The union of the head and shaft compose the screw.
  head();
  shaft();

}

gasket();
translate([gasket_d + screw_inset, gasket_d + screw_inset, 0]) screw();
translate([inner_x + gasket_d - screw_inset, gasket_d + screw_inset, 0]) screw();
translate([gasket_d + screw_inset, inner_y + gasket_d - screw_inset, 0]) screw();
translate([inner_x + gasket_d - screw_inset, inner_y + gasket_d - screw_inset, 0]) screw();

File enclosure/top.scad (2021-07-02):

/* Top portion of the enclosure for:
 * Sequential Turn Signal
 *
 * This part can be constructed out of metal, plastic, or wood,
 * but metal is recommended.  The enclosure should be mounted in
 * a dry, well-ventilated area as it will not prevent moisture
 * ingress or provide thermal insulation for the electronics.
 */

inner_x = 160;          // Interior dimension of enclosure in x direction.
inner_y = 100;          // Interior dimension of enclosure in y direction.
inner_z = 20;           // Interior dimension of enclosure in z direction.
inner_z_min = 10;        // Minimum distance between top of enclosure and PCB.
wall_d = 4;             // Enclosure wall thickness.
mount_r = 3;            // Radius of PCB mounting posts.
screw_inset = 6;        // Distance from closest edge of PCB to center of screw.
screw_r = 3;            // Screw head radius.
thread_outer_r = 2.182; // Mounting screw outer radius.
pwr_inset_x = 11;       // Size of power connector in x direction.
pwr_inset_y = 23;       // Size of power connector in the y direction.
pwr_offset = 13;        // Offset from origin along y axis to power connector.
sig_inset_x = 11;       // Size of signal connector in x direction.
sig_inset_y = 33;       // Size of signal connector in y direction.
sig_offset = 53;        // Offset from origin along y axis to signal connector.
eps = 0.001;            // Epsilon constant to ensure overlap for difference().

// The top portion of the enclosure.
module top()
{

  // Exterior shell of the top of the enclosure.
  module exterior()
  {
    difference()
    {
      cube([inner_x + 2 * wall_d, inner_y + 2 * wall_d, inner_z + wall_d]);
      translate([-eps, pwr_offset + wall_d, -eps])
      {
        cube([pwr_inset_x + eps, pwr_inset_y, inner_z + wall_d + 2 * eps]);
      }
      translate([-eps, sig_offset + wall_d, -eps]) {
         cube([sig_inset_x + eps, sig_inset_y, inner_z + wall_d + 2 * eps]);
      }
    }
  }

  // Mounting stub which contacts the PCB at the screw holes.
  module mount()
  {
    translate([0, 0, inner_z_min])
    {
      cylinder(r=screw_r + wall_d, h=inner_z_min);
    }
    cylinder(r=mount_r, h=inner_z);
  }

  // Interior volume of the top of the enclosure.
  module interior()
  {
    difference()
    {
      translate([0, 0, -eps]) cube([inner_x, inner_y, inner_z + eps]);
      translate([-eps, pwr_offset - wall_d, -2 * eps])
      {
        cube([pwr_inset_x + eps, pwr_inset_y + 2 * wall_d, inner_z + 4 * eps]);
      }
      translate([-eps, sig_offset - wall_d, -2 * eps])
      {
        cube([sig_inset_x + eps, sig_inset_y + 2 * wall_d, inner_z + 4 * eps]);
      }
      translate([screw_inset, screw_inset, 0]) mount();
      translate([inner_x - screw_inset, screw_inset, 0]) mount();
      translate([screw_inset, inner_y - screw_inset, 0]) mount();
      translate([inner_x - screw_inset, inner_y - screw_inset, 0]) mount();
    }
  }

  // Holes for screws to attach the top and bottom portions of the enclosure.
  module screw_holes()
  {

    // Screw hole centered on the origin.
    module hole()
    {
      translate([0, 0, inner_z_min + wall_d])
      {
        cylinder(r=screw_r, h=inner_z_min + wall_d);
      }
      translate([0, 0, -eps])
      {
        cylinder(r=thread_outer_r, h=inner_z + wall_d + eps);
      }
    }

    // Copy the hole at the correct locations.
    translate([screw_inset, screw_inset, 0]) hole();
    translate([inner_x - screw_inset, screw_inset, 0]) hole();
    translate([screw_inset, inner_y - screw_inset, 0]) hole();
    translate([inner_x - screw_inset, inner_y - screw_inset, 0]) hole();

  }

  /* Construct the top portion of the enclosure by removing the interior
   * volume and the screw holes from the volume bounded by the exterior.
   */
  difference()
  {
    exterior();
    translate([wall_d, wall_d, 0]) interior();
    translate([wall_d, wall_d, 0]) screw_holes();
  }

}

top();

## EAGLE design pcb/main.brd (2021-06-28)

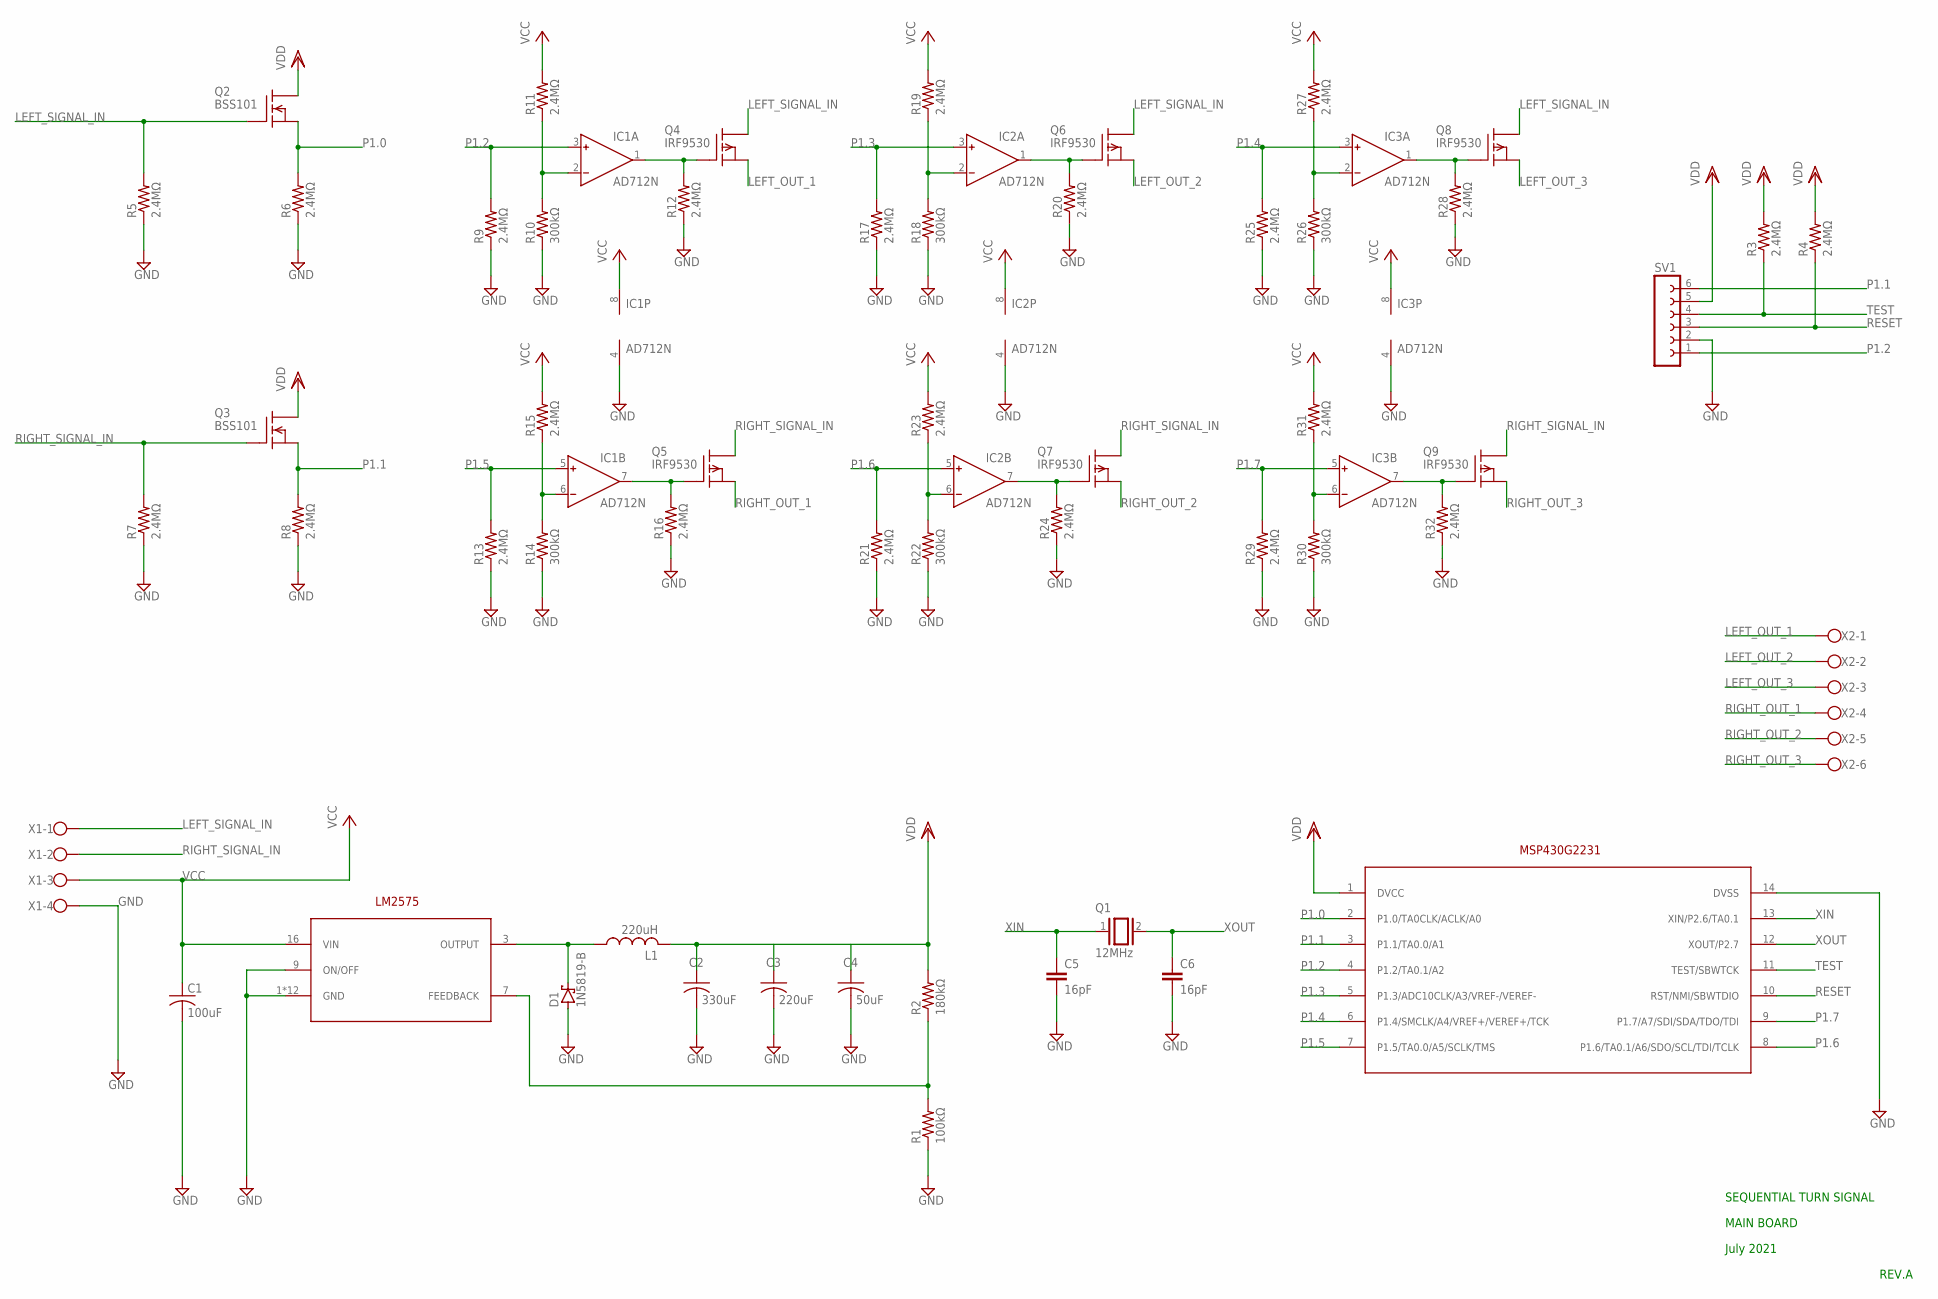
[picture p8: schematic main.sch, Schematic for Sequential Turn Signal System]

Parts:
C1: 100uF; C025-050X050
C2: 330uF; C025-050X050
C3: 220uF; C025-050X050
C4: 50uF; C025-050X050
C5, C6: 16pF; C025-024X044
D1: 1N5819-B; DO41-7.6
IC1, IC2, IC3: AD712N; DIL08
L1: 220uH; 6000-XXXX-RC
Q1: 12MHz; Q
Q2, Q3: BSS101; TO92
Q4, Q5, Q6, Q7, Q8, Q9: IRF9530; TO220
R1: 100kΩ; 0207/12
R2: 180kΩ; 0207/12
R3, R4, R5, R6, R7, R8, R9, R11, R12, R13, R15, R16, R17, R19, R20, R21, R23, R24, R25, R27, R28, R29, R31, R32: 2.4MΩ; 0207/12
R10, R14, R18, R22, R26, R30: 300kΩ; 0207/12
SV1: FE06-1; FE06
U$1: MSP430G2231PDIP14; DIP762W53P254L1969H508Q14B
U$2: LM2575PDIP16; DIP762W53P254L1969H508Q16B
X1: W237-4
X2: W237-6

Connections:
GND: C1.2, C2.2, C3.2, C4.2, C5.2, C6.2, D1.A, IC1.4 (V-), IC2.4 (V-), IC3.4 (V-), R1.1, R5.1, R6.1, R7.1, R8.1, R9.1, R10.1, R12.1, R13.1, R14.1, R16.1, R17.1, R18.1, R20.1, R21.1, R22.1, R24.1, R25.1, R26.1, R28.1, R29.1, R30.1, R32.1, SV1.2, U$1.14 (DVSS), U$2.1 (GND), U$2.2 (GND), U$2.4 (GND), U$2.5 (GND), U$2.6 (GND), U$2.8 (GND), U$2.9 (ON/OFF), U$2.10 (GND), U$2.11 (GND), U$2.12 (GND), U$2.13 (GND), U$2.14 (GND), U$2.15 (GND), X1.4
LEFT_OUT_1: Q4.3 (S), X2.1
LEFT_OUT_2: Q6.3 (S), X2.2
LEFT_OUT_3: Q8.3 (S), X2.3
LEFT_SIGNAL_IN: Q2.2 (G), Q4.2 (D), Q6.2 (D), Q8.2 (D), R5.2, X1.1
unnamed: D1.C, L1.1, U$2.3 (OUTPUT)
unnamed: R1.2, R2.1, U$2.7 (FEEDBACK)
unnamed: IC1.6 (IN-), R14.2, R15.1
unnamed: IC1.7 (OUT), Q5.1 (G), R16.2
unnamed: IC1.1 (OUT), Q4.1 (G), R12.2
unnamed: IC1.2 (IN-), R10.2, R11.1
unnamed: IC2.6 (IN-), R22.2, R23.1
unnamed: IC2.7 (OUT), Q7.1 (G), R24.2
unnamed: IC2.1 (OUT), Q6.1 (G), R20.2
unnamed: IC2.2 (IN-), R18.2, R19.1
unnamed: IC3.6 (IN-), R30.2, R31.1
unnamed: IC3.7 (OUT), Q9.1 (G), R32.2
unnamed: IC3.1 (OUT), Q8.1 (G), R28.2
unnamed: IC3.2 (IN-), R26.2, R27.1
P1.0: Q2.1 (S), R6.2, U$1.2 (P1.0/TA0CLK/ACLK/A0)
P1.1: Q3.1 (S), R8.2, SV1.6, U$1.3 (P1.1/TA0.0/A1)
P1.2: IC1.3 (IN+), R9.2, SV1.1, U$1.4 (P1.2/TA0.1/A2)
P1.3: IC2.3 (IN+), R17.2, U$1.5 (P1.3/ADC10CLK/A3/VREF-/VEREF-)
P1.4: IC3.3 (IN+), R25.2, U$1.6 (P1.4/SMCLK/A4/VREF+/VEREF+/TCK)
P1.5: IC1.5 (IN+), R13.2, U$1.7 (P1.5/TA0.0/A5/SCLK/TMS)
P1.6: IC2.5 (IN+), R21.2, U$1.8 (P1.6/TA0.1/A6/SDO/SCL/TDI/TCLK)
P1.7: IC3.5 (IN+), R29.2, U$1.9 (P1.7/A7/SDI/SDA/TDO/TDI)
RESET: R4.1, SV1.3, U$1.10 (RST/NMI/SBWTDIO)
RIGHT_OUT_1: Q5.3 (S), X2.4
RIGHT_OUT_2: Q7.3 (S), X2.5
RIGHT_OUT_3: Q9.3 (S), X2.6
RIGHT_SIGNAL_IN: Q3.2 (G), Q5.2 (D), Q7.2 (D), Q9.2 (D), R7.2, X1.2
TEST: R3.1, SV1.4, U$1.11 (TEST/SBWTCK)
VCC: C1.1, IC1.8 (V+), IC2.8 (V+), IC3.8 (V+), R11.2, R15.2, R19.2, R23.2, R27.2, R31.2, U$2.16 (VIN), X1.3
VDD: C2.1, L1.2, Q2.3 (D), Q3.3 (D), R2.2, R3.2, R4.2, SV1.5, U$1.1 (DVCC)
VDD1: C3.1
VDD2: C4.1
XIN: C5.1, Q1.1, U$1.13 (XIN/P2.6/TA0.1)
XOUT: C6.1, Q1.2, U$1.12 (XOUT/P2.7)

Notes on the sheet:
SEQUENTIAL TURN SIGNAL
MAIN BOARD
July 2021
REV.A

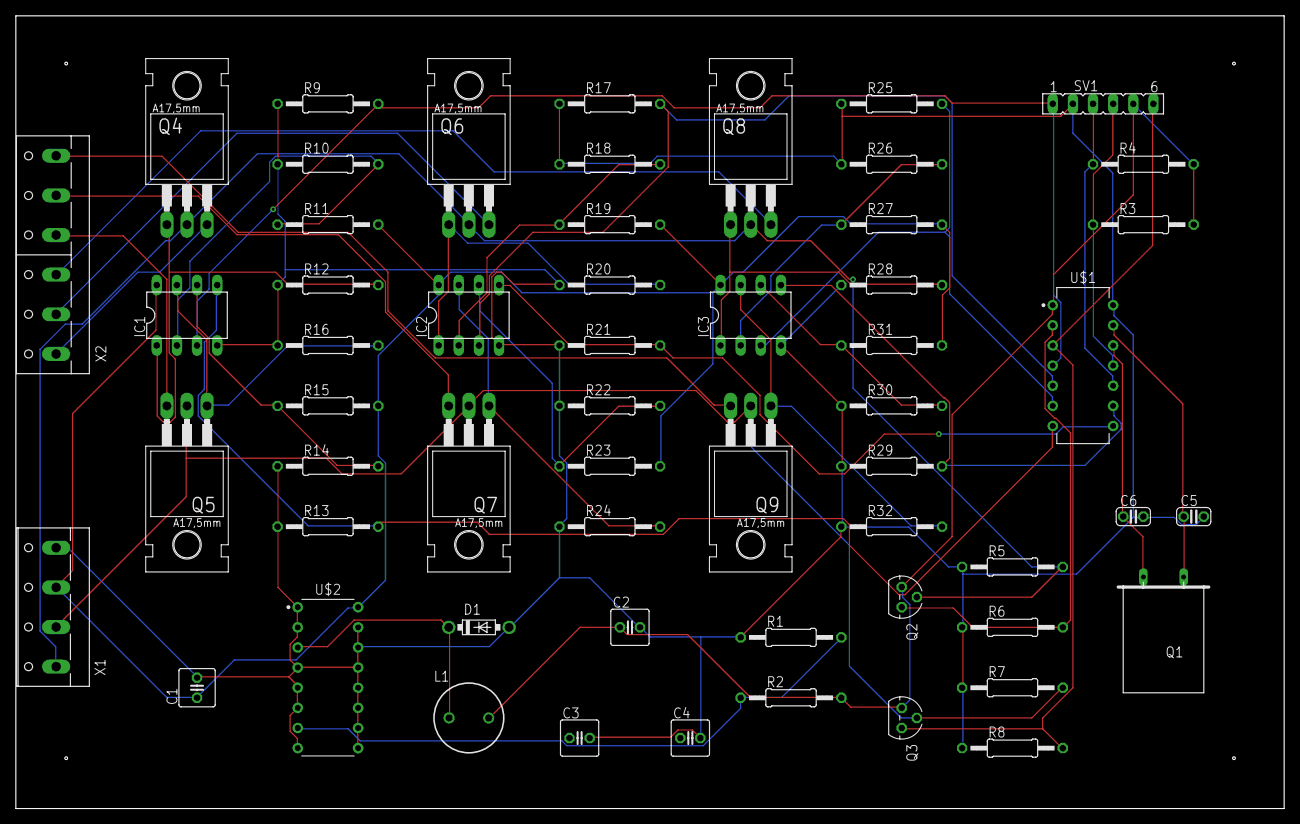
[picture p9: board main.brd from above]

Board: 2 copper layers, 160.0 x 100.0 mm, 57 parts (0 on the bottom side), 37 nets.

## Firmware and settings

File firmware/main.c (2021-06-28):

/*
 * Sequential Turn Signal - main.c
 * This file contains the microcontroller code to implement sequential turn signals on the Corvette
 * (c) 2017 Michael Yuhas
 */

/*
 * Includes:
 * msp430.h - constants and pin mappings for msp430
 */
#include <msp430.h>

/*
 * Definitions:
 * TIMER_RESOLUTION_MS - resolution of turn signal timer in milliseconds
 * TIMER_RESOLUTION_TICKS - resolution of turn signal timer in ticks of timer A
 * P1_INPUT_MASK - input bits on port 1
 * P1_RESET_INTERRUPT_FLAG - reset value for port 1
 * LEFT_SIGNAL - output bits for the left turn signal on port 1
 * LEFT_SIGNAL_1_MASK - output bits for left turn signal pattern 1
 * LEFT_SIGNAL_2_MASK - output bits for left turn signal pattern 2
 * LEFT_SIGNAL_3_MASK - output bits for left turn signal pattern 3
 * LEFT_SIGNAL_4_MASK - output bits for left turn signal pattern 4
 * LEFT_SIGNAL_ALL_MASK - all lights in left signal set to active
 * LEFT_INPUT_MASK - input bit that controls the left turn signal
 * RIGHT_SIGNAL - output bits for the right turn signal on port 1
 * RIGHT_SIGNAL_1_MASK - output bits for right turn signal pattern 1
 * RIGHT_SIGNAL_2_MASK - output bits for right turn signal pattern 2
 * RIGHT_SIGNAL_3_MASK - output bits for right turn signal pattern 3
 * RIGHT_SIGNAL_4_MASK - output bits for right turn signal pattern 4
 * RIGHT_SIGNAL_ALL_MASK - all lights in right signal set to active
 * RIGHT_INPUT_MASK - input bit that controls the right turn signal
 */
#define TIMER_RESOLUTION_MS		1
#define TIMER_RESOLUTION_TICKS	125 * TIMER_RESOLUTION_MS
#define P1_INPUT_MASK			0xC0
#define P1_RESET_INTERRUPT_FLAG 0x00
#define LEFT_SIGNAL				0x38
#define LEFT_SIGNAL_1_MASK		0x30
#define LEFT_SIGNAL_2_MASK		0x28
#define LEFT_SIGNAL_3_MASK		0x18
#define LEFT_SIGNAL_4_MASK		0x00
#define	LEFT_SIGNAL_ALL_MASK	0x00
#define LEFT_INPUT_MASK			0x80
#define RIGHT_SIGNAL			0x07
#define RIGHT_SIGNAL_1_MASK		0x03
#define RIGHT_SIGNAL_2_MASK		0x05
#define RIGHT_SIGNAL_3_MASK		0x06
#define RIGHT_SIGNAL_4_MASK		0x00
#define RIGHT_SIGNAL_ALL_MASK	0x00
#define RIGHT_INPUT_MASK		0x40

/*
 * Typedefs:
 * State - corresponds to the current output pattern of a turn signal
 */
typedef enum { INIT, PATTERN_1, PATTERN_2, PATTERN_3, PATTERN_4 } State;

/*
 * Globals:
 * tick_count - current number of TIMER_RESOLUTION_MS length ticks that have passed
 * input_vector - vector of the input port, set by port 1 interrupt
 */
unsigned int tick_count;
unsigned char input_vector;

/*
 * port_one_interrupt - this function executes everytime an interrupt event occurs on P1
 * arguments:
 * (none)
 * returns:
 * (none)
 */
#pragma vector=PORT1_VECTOR
__interrupt void port_one_interrupt( void )
{
  input_vector = P1IN & P1_INPUT_MASK;
  P1IES = input_vector;
  P1IFG = P1_RESET_INTERRUPT_FLAG;
  __bic_SR_register_on_exit( LPM0_bits );
  return;
}

/*
 * timer_a_interrupt - this function executes everytime timer A reaches the value in CCR0
 * arguments:
 * (none)
 * returns:
 * (none)
 */
#pragma vector=TIMERA0_VECTOR
__interrupt void timer_a_interrupt( void )
{
  TACTL = MC_0;
  tick_count++;
  CCR0 = TIMER_RESOLUTION_TICKS;
  TAR = 0;
  TACTL = TASSEL_2 | ID_3 | MC_1;
  __bic_SR_register_on_exit( LPM0_bits );
  return;
}

/*
 * left_state_machine - this function keeps track of the left turn signal state machine
 * arguments:
 * *left_state - pointer to current state
 * *next_left - pointer to an integer representing the next time for a state change
 * tick_count - current tick count of the timer
 * wait_time - amount of time to wait (in ticks) between a state change
 * returns:
 * (none)
 */
void left_state_machine( State *left_state, unsigned int *next_left, unsigned int tick_count, unsigned int wait_time )
{
  // Moore type state machine
  switch ( *left_state )
  {
    // Initialization state
    case INIT :
      // Check if the left turn signal was activated
      if ( ( input_vector & LEFT_INPUT_MASK ) == LEFT_INPUT_MASK )
      {
        *left_state = PATTERN_1;
        *next_left = tick_count + wait_time;
        P1OUT = ( P1OUT & RIGHT_SIGNAL ) | LEFT_SIGNAL_1_MASK;
        // If the timer hasn't been started yet, start the timer
        if ( TACTL == MC_0 )
        {
          TAR = 0;
          CCR0 = TIMER_RESOLUTION_TICKS;
          TACTL = TASSEL_2 + ID_3 + MC_1;
        }
      }
      break;
    // Pattern 1 on left signal
    case PATTERN_1 :
      // Check if the left turn signal was turned off
      if ( ( input_vector & LEFT_INPUT_MASK ) != LEFT_INPUT_MASK )
      {
        *left_state = INIT;
        P1OUT = ( P1OUT & RIGHT_SIGNAL ) | LEFT_SIGNAL_ALL_MASK;
        return;
      }
      // Check if the time limit in Pattern 1 was reached, if so proceed to pattern 2
      if ( tick_count == *next_left )
      {
        *left_state = PATTERN_2;
        *next_left = tick_count + wait_time;
        P1OUT = ( P1OUT & RIGHT_SIGNAL ) | LEFT_SIGNAL_2_MASK;
      }
      break;
    // Pattern 2 on left signal
    case PATTERN_2 :
      // Check if the left turn signal was turned off
      if ( ( input_vector & LEFT_INPUT_MASK ) != LEFT_INPUT_MASK )
      {
        *left_state = INIT;
        P1OUT = ( P1OUT & RIGHT_SIGNAL ) | LEFT_SIGNAL_ALL_MASK;
        return;
      }
      // Check if the time limit in Pattern 2 was reached, if so proceed to pattern 3
      if ( tick_count == *next_left )
      {
        *left_state = PATTERN_3;
        *next_left = tick_count + wait_time;
        P1OUT = ( P1OUT & RIGHT_SIGNAL ) | LEFT_SIGNAL_3_MASK;
      }
      break;
    // Pattern 3 on left signal
    case PATTERN_3 :
      // Check if the left turn signal was turned off
      if ( ( input_vector & LEFT_INPUT_MASK ) != LEFT_INPUT_MASK )
      {
        *left_state = INIT;
        P1OUT = ( P1OUT & RIGHT_SIGNAL ) | LEFT_SIGNAL_ALL_MASK;
        return;
      }
      // Check if the time limit in Pattern 3 was reached, if so proceed to pattern 4
      if ( tick_count == *next_left )
      {
        *left_state = PATTERN_4;
        *next_left = tick_count + wait_time;
        P1OUT = ( P1OUT & RIGHT_SIGNAL ) | LEFT_SIGNAL_4_MASK;
      }
      break;
    // Pattern 4 on left signal
    case PATTERN_4 :
      // Check if the left turn signal was turned off
      if ( ( input_vector & LEFT_INPUT_MASK ) != LEFT_INPUT_MASK )
      {
        *left_state = INIT;
        P1OUT = ( P1OUT & RIGHT_SIGNAL ) | LEFT_SIGNAL_ALL_MASK;
        return;
      }
      break;
    // Default case: reset to Initialization
    default :
      *left_state = INIT;
      P1OUT = ( P1OUT & RIGHT_SIGNAL ) | LEFT_SIGNAL_ALL_MASK;
      break;
  }
  return;
}

/*
 * right_state_machine - this function keeps track of the right turn signal state machine
 * arguments:
 * *right_state - pointer to current state
 * *next_right - pointer to an integer representing the next time for a state change
 * tick_count - current tick count of the timer
 * wait_time - amount of time to wait (in ticks) between a state change
 * returns:
 * (none)
 */
void right_state_machine( State *right_state, unsigned int *next_right, unsigned int tick_count, unsigned int wait_time )
{
  // Moore type state machine
  switch ( *right_state )
  {
    // Initialization state
    case INIT :
      // Check if the right turn signal was activated
      if ( ( input_vector & RIGHT_INPUT_MASK ) == RIGHT_INPUT_MASK )
      {
        *right_state = PATTERN_1;
        *next_right = tick_count + wait_time;
        P1OUT = ( P1OUT & LEFT_SIGNAL ) | RIGHT_SIGNAL_1_MASK;
        // If the timer hasn't been started yet, start the timer
        if ( TACTL == MC_0 )
        {
          TAR = 0;
          CCR0 = TIMER_RESOLUTION_TICKS;
          TACTL = TASSEL_2 + ID_3 + MC_1;
        }
      }
      break;
    // Pattern 1 on right signal
    case PATTERN_1 :
      // Check if the right turn signal was turned off
      if ( ( input_vector & RIGHT_INPUT_MASK ) != RIGHT_INPUT_MASK )
      {
        *right_state = INIT;
        P1OUT = ( P1OUT & LEFT_SIGNAL ) | RIGHT_SIGNAL_ALL_MASK;
        return;
      }
      // Check if the time limit in Pattern 1 was reached, if so proceed to pattern 2
      if ( tick_count == *next_right )
      {
        *right_state = PATTERN_2;
        *next_right = tick_count + wait_time;
        P1OUT = ( P1OUT & LEFT_SIGNAL ) | RIGHT_SIGNAL_2_MASK;
      }
      break;
    // Pattern 2 on right signal
    case PATTERN_2 :
      // Check if the right turn signal was turned off
      if ( ( input_vector & RIGHT_INPUT_MASK ) != RIGHT_INPUT_MASK )
      {
        *right_state = INIT;
        P1OUT = ( P1OUT & LEFT_SIGNAL ) | RIGHT_SIGNAL_ALL_MASK;
        return;
      }
      // Check if the time limit in Pattern 2 was reached, if so proceed to pattern 3
      if ( tick_count == *next_right )
      {
        *right_state = PATTERN_3;
        *next_right = tick_count + wait_time;
        P1OUT = ( P1OUT & LEFT_SIGNAL ) | RIGHT_SIGNAL_3_MASK;
      }
      break;
    // Pattern 3 on right signal
    case PATTERN_3 :
      // Check if the right turn signal was turned off
      if ( ( input_vector & RIGHT_INPUT_MASK ) != RIGHT_INPUT_MASK )
      {
        *right_state = INIT;
        P1OUT = ( P1OUT & LEFT_SIGNAL ) | RIGHT_SIGNAL_ALL_MASK;
        return;
      }
      // Check if the time limit in Pattern 2 was reached, if so proceed to pattern 4
      if ( tick_count == *next_right )
      {
        *right_state = PATTERN_4;
        *next_right = tick_count + wait_time;
        P1OUT = ( P1OUT & LEFT_SIGNAL ) | RIGHT_SIGNAL_4_MASK;
      }
      break;
    // Pattern 4 on right signal
    case PATTERN_4 :
      // Check if the right turn signal was turned off
      if ( ( input_vector & RIGHT_INPUT_MASK ) != RIGHT_INPUT_MASK )
      {
        *right_state = INIT;
        P1OUT = ( P1OUT & LEFT_SIGNAL ) | RIGHT_SIGNAL_ALL_MASK;
        return;
      }
      break;
    // Default case: reset to Initialization
    default :
      *right_state = INIT;
      P1OUT = ( P1OUT & LEFT_SIGNAL ) | RIGHT_SIGNAL_ALL_MASK;
      break;
  }
  return;
}


/*
 * main - code entry point
 * arguments:
 * (none)
 * returns:
 * (none)
 */
void main( void )
{
  WDTCTL = WDTPW | WDTHOLD;
  P1REN = 0x00;
  P1SEL = 0x00;
  P1DIR = 0x3F;
  P1OUT = 0x00;
  P1IES = 0x00;
  P1IFG = 0x00;
  P1IE = 0xC0;
  TACTL = MC_0;
  CCTL0 |= CCIE;
  input_vector = 0x00;
  State left_state = INIT;
  State right_state = INIT;
  unsigned int next_left = 0;
  unsigned int next_right = 0;
  unsigned int wait_time = 200;
  WDTCTL = WDTPW | WDT_MRST_8;
  __enable_interrupt();
  // Calculate Next State -> Set Outputs -> Sleep
  while ( 1 )
  {
    WDTCTL = WDTPW | WDTCNTCL | WDT_MRST_8;
    left_state_machine( &left_state, &next_left, tick_count, wait_time);
    right_state_machine( &right_state, &next_right, tick_count, wait_time);
    __bis_SR_register( LPM0_bits + GIE );
  }
}

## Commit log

2017-02-12 Committing Code Changes
    Working on State Machine, currently failing linking
    [main.c]
2017-04-05 Playing with Cadsoft Eagle
    Playing with Cadsoft Eagle
    [main.sch]
2017-04-13 Refactored Code
    Now State Machines Run in Main, with interrupts passing info via globals
2017-09-20 Adding watchdog timer for safety
2019-04-01 Moving schematic to top level
    [main.sch, schematic.sch]
2021-06-28 uploading finished schematic and board layout
    [main.brd, main.sch]
2021-06-28 removing duplicate files
    [schematic.sch]
2021-06-30 Adding 1st SCAD model
    [bottom.scad]
2021-07-01 drafts of enclosure
    [gasket.scad, top.scad]
2021-07-02 finishing touches on CAD models
    [bottom.scad, gasket.scad, top.scad]
